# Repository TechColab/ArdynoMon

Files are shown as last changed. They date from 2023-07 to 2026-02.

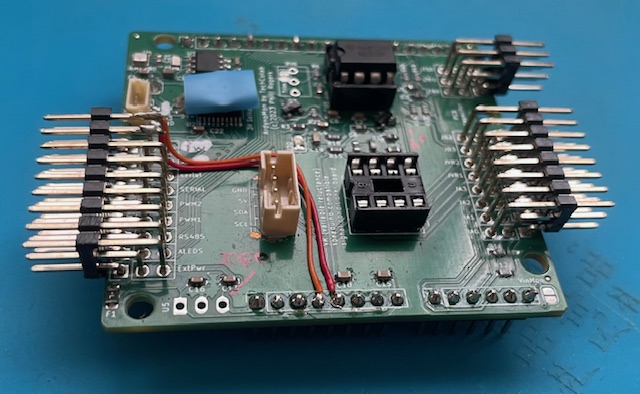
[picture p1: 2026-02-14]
ArdynoMon-ProtoMod.jpeg

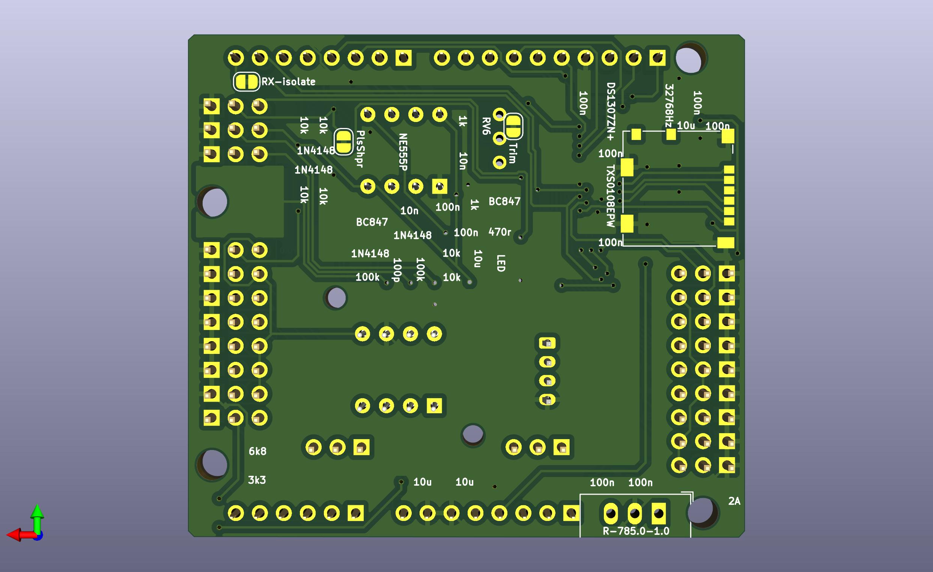
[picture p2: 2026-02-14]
ArdynoMon-B.jpg

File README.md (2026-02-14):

# ArdynoMon
Arduino shield for DIY dynos, engine monitoring &amp; more.  
Designed for monitoring & logging key aspects of an internal combustion engine for the purpose of R&D for my own Engine Management system. 
Aims to be the natural successor for the "Ardyno" shield https://ardyno.weebly.com/ with more input options & logging.  

Basically, it uses the Arduino's two interrupts to accuately record one or two channels of engine cycle events.  
While the original Ardyno would use one signal from an inertia drum roller & one signal from the ignition system, this ArdynoMon can alternatively be used to get both signals from different parts of the ignition system.  

# 2023-02-14 Revision 3.6 addresses all know issues.
    After some external interest (thank you) I've been nudged into refreshing this page.  
	I still get a bit lost with KiCAD files so if I've missed one from the upload, let me know.  
    Amusingly, I have recently used it to check th timing of a minimal EVSE (EV charger) I've built.  

# 2023-07-31 Don't use this version.
    Significant updated coming shortly to address the following issues with this version:  
	I accepted a subtitution of the transistors without realising that they have a different pinout.  
 	The RX going through the level shifter prevents in-situ programming.  
  	Better to choose the regulator on the Arduino *OR* the one on ArdynoMon shield, but not both!  
   	Both 1-Wire busses need a power pin as passive power is not always wanted.  

## 1.) updates from Ardyno Rev1  
	- drop A4 & A5 reducing on-board analogue inputs from 6 to 4.  
	+ frees I2C to go with UART & SPI  
	+ accept 1-wire digital temperature sensors (both 5V & 3.3V) bus powered or not  
	+ accept trigger from coil primary. Option for lo-V (5-12V COP) or hi-V (400V CDI/IDI)  
	+ accept trigger from 12V (& 5V) Hall effect sensors with suitable protection. Rising or Falling edge    
	+ option for VR conditioner / Opto-isolator plug-in board  
		E.g. in addition to coil primary trigger for measuring dwell time  
	+ gives 2 digital I/Os for PWM, servo, Dir+Step, analogue output etc.
		E.g. PWM eddie current brake & servo throttle  
		E.g. foot-switch to trigger logging time-stamp 'way-point'  
	+ better use of coastline with 3-pin 90-degree pin headers, can also use IDC ribbon cable connectors  
	+ all key signals are 3V & 5V  
	+ replace 555 timing C & R with 1nF (as close as poss) & 1k + optional 2M trim-pot for variable pulse width  
	+ put LED on output of 555 to aid diagnosing pick-ups which use it  
	= wider audience, upgradable, inline with YourDyno  

## 2.) additional monitoring features integrated
	+ uSD/TF on SPI, sharable with other SPI devices
	+ ambient humidity, air pressure, temperature on I2C  
	+ RTC on I2C  
	+ jumper option with resistor divider to measure vehicle battery voltage
	= fully integrated logger (not just ArdynoMon) better than existing one. Can share SPI, doesn't use analogue pins  

## 3.) designed-for optional ad-hoc add-ons
	drive individually addressable RGB LEDs for rev-counter & other indicators etc.
	serial logging via Bluetooth or WiFi module. On pigtails to get out of Faraday cage  
	current sensor on COP to find required dwell time - to one of the analogue inputs  
	RS485 bus for multi-drop peripheral/controller  
	1-wire: DS18b20, K-type thermocouple amplifiers, battery monitor  
	I2C: 24-bit ADC strain-guage amplifier, IMU  
	SPI: CAN bus?
	published (push-pull buffered) sync pulse from conditioned signal. For tacho, etc. (crank & cycle)  
	can drive high power COB LEDs via MOSFET for simple ignition strobe light  

# Uses:

Monitor the ignition trigger pick-up & the coil to capture the advance/retard curve of the CDI/IDI system.  
Monitor the coil primary to capture the dwell time variation of an induction (IDI) system.  
Monitor the RPM & drive an LED ring for rev-counter with MOSFET for rev-limmiter or auto-shift.  
Add supplimental injection system: N2O, H2O etc.

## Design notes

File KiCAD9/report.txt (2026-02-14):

Plotted to '/media/phill/Data/Documents/kicad/ArdynoMon/Gerbers/ArdynoMon-F_Cu.gbr'.
Plotted to '/media/phill/Data/Documents/kicad/ArdynoMon/Gerbers/ArdynoMon-B_Cu.gbr'.
Plotted to '/media/phill/Data/Documents/kicad/ArdynoMon/Gerbers/ArdynoMon-F_Silkscreen.gbr'.
Plotted to '/media/phill/Data/Documents/kicad/ArdynoMon/Gerbers/ArdynoMon-B_Silkscreen.gbr'.
Created Gerber job file '/media/phill/Data/Documents/kicad/ArdynoMon/Gerbers/ArdynoMon-job.gbrjob'.
Info: Done.
Info: Done.

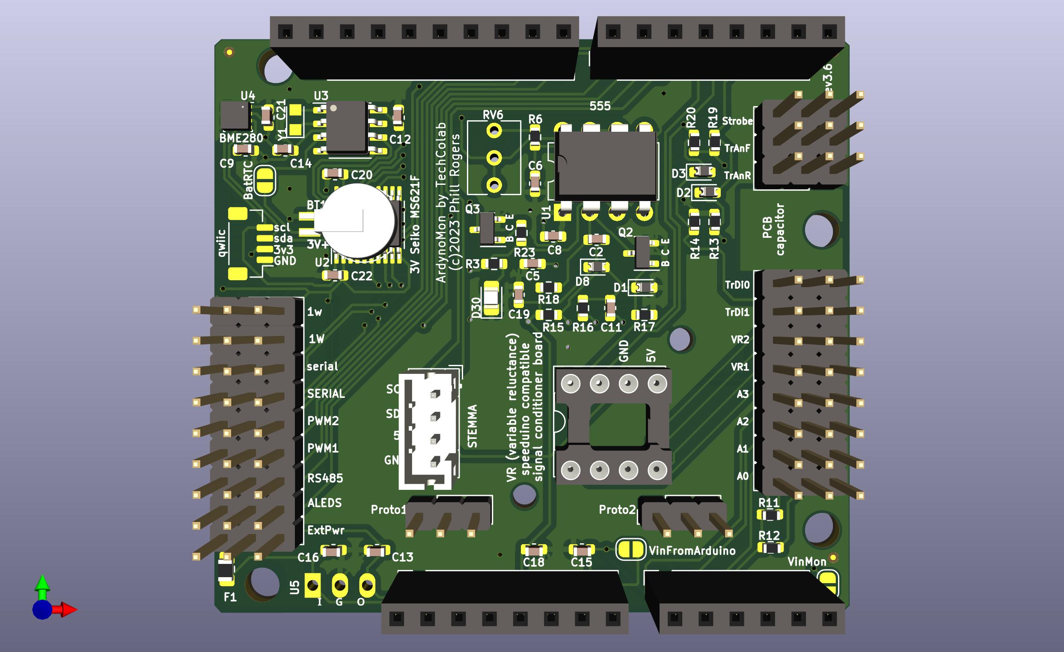
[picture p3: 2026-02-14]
ArdynoMon-F.jpg

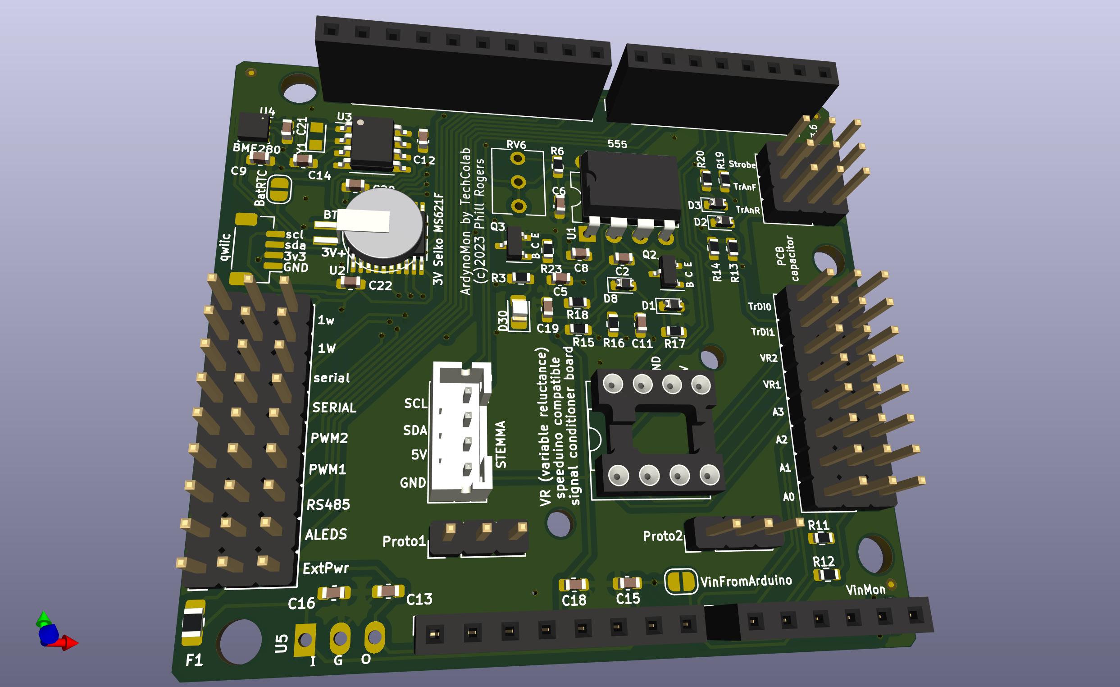
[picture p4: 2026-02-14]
ArdynoMon-Fangled.jpg

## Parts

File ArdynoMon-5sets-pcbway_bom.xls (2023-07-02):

PCBWay Bom Quotation, Product No.:T-1F6W473013A
Item # | *Designator | *Qty | Manufacturer | *Mfg Part # | Description / Value | *Package/Footprint | Mounting Type | *Unit Price(5 sets) | *Total | *Delivery Time | *Actual Purchase Mfg Part # | *PCBWay Note | Customer Reply | PCBWay Update
1 | BT1 | 1 |  |  | 3V Seiko MS621F | BatteryHolder_Seiko_MS621F | smt |  |  |  |  | [DNP不要贴];
2 | C11 | 1 | YAGEO |  | 100p | C_0603_1608Metric | smt | $0.058 | $0.290 |  | CC0603JRNPO9BN101
3 | C12, C13, C16, C20, C21, C22, C5, C8, C9 | 9 | YAGEO |  | 100n | C_0603_1608Metric | smt | $0.007 | $0.315 |  | CC0603KRX7R9BB104
4 | C14, C15, C18, C19 | 4 | YAGEO |  | 10u | C_0603_1608Metric | smt | $0.129 | $2.580 |  | CC0603MRX5R8BB106
5 | C2, C6 | 2 | YAGEO |  | 10n | C_0603_1608Metric | smt | $0.021 | $0.210 |  | CC0603KRX7R9BB103
6 | D1, D2, D3, D8 | 4 | Taiwan Semiconductor Corporation |  | 1N4148 | D_0603_1608Metric | smt | $0.286 | $5.720 | 7-10 Workdays | TS4148C RCG
7 | D30 | 1 | LITEON |  | LED | LED_0805_2012Metric_Pad1.15x1.40mm_HandSolder | smt | $0.233 | $1.165 |  | LTST-C191TBKT | Color: BLUE
8 | F1 | 1 | Littelfuse Inc. |  | 2A | Fuse_0805_2012Metric_Pad1.15x1.40mm_HandSolder | smt | $0.653 | $3.265 |  | 0805L200SLTHYR
9 | FID1, FID2, FID3 | 3 |  |  | Fiducial | Fiducial_0.5mm_Mask1mm | smt |  |  |  |  | [DNP不要贴];
10 | J11 | 1 |  |  | VR board | DIP-8_W7.62mm_Socket | tht |  |  |  |  | [DNP不要贴];
11 | J13 | 1 | Ckmtw |  | Proto | PinHeader_1x03_P2.54mm_Vertical | tht |  |  |  | B-2100S03P-A110 | [DNP不要贴];
12 | J14 | 1 | Molex |  | Micro_SD_Card_Det_Hirose_DM3AT | microSD_HC_Molex_104031-0811 | smt | $0.849 | $4.245 |  | 104031-0811
13 | J15 | 1 | Ckmtw |  | ExtPwr | PinHeader_1x03_P2.54mm_Vertical | tht |  |  |  | B-2100S03P-A110 | [DNP不要贴];
14 | J17 | 1 | HCTL |  | Power | PinSocket_1x08_P2.54mm_Vertical | tht |  |  |  | PM254-1-08-Z-8.5 | [DNP不要贴];
15 | J18 | 1 | XFCN |  | Analog | PinSocket_1x06_P2.54mm_Vertical | tht |  |  |  | PM254V-11-06-H85 | [DNP不要贴];
16 | J19 | 1 | HCTL |  | Digital/PWM | PinSocket_1x10_P2.54mm_Vertical | tht |  |  |  | PM254-1-10-Z-8.5 | [DNP不要贴];
17 | J20 | 1 | HCTL |  | Digital/PWM | PinSocket_1x08_P2.54mm_Vertical | tht |  |  |  | PM254-1-08-Z-8.5 | [DNP不要贴];
18 | J21 | 1 | JST Sales America Inc. |  | qwiic | JST_SH_BM04B-SRSS-TB_1x04-1MP_P1.00mm_Vertical | smt | $0.392 | $1.960 |  | BM04B-SRSS-TB(LF)(SN)
19 | J22 | 1 | JST Sales America Inc. |  | STEMMA | JST_PH_B4B-PH-K_1x04_P2.00mm_Vertical | tht | $0.202 | $1.010 |  | B4B-PH-K(LF)(SN)
20 | J23 | 1 | Ckmtw |  | serial | PinHeader_1x03_P2.54mm_Vertical | tht |  |  |  | B-2100S03P-A110 | [DNP不要贴];
21 | JA0 | 1 | Ckmtw |  | A0 | PinHeader_1x03_P2.54mm_Vertical | tht |  |  |  | B-2100S03P-A110 | [DNP不要贴];
22 | JA1 | 1 | Ckmtw |  | A1 | PinHeader_1x03_P2.54mm_Vertical | tht |  |  |  | B-2100S03P-A110 | [DNP不要贴];
23 | JA2 | 1 | Ckmtw |  | A2 | PinHeader_1x03_P2.54mm_Vertical | tht |  |  |  | B-2100S03P-A110 | [DNP不要贴];
24 | JA3 | 1 | Ckmtw |  | A3 | PinHeader_1x03_P2.54mm_Vertical | tht |  |  |  | B-2100S03P-A110 | [DNP不要贴];
25 | JD10 | 1 | Ckmtw |  | PWM2 | PinHeader_1x03_P2.54mm_Vertical | tht |  |  |  | B-2100S03P-A110 | [DNP不要贴];
26 | JD2 | 1 | Ckmtw |  | TrDi0 | PinHeader_1x03_P2.54mm_Vertical | tht |  |  |  | B-2100S03P-A110 | [DNP不要贴];
27 | JD23 | 1 | Ckmtw |  | SERIAL | PinHeader_1x03_P2.54mm_Vertical | tht |  |  |  | B-2100S03P-A110 | [DNP不要贴];
28 | JD3 | 1 | Ckmtw |  | TrDi1 | PinHeader_1x03_P2.54mm_Vertical | tht |  |  |  | B-2100S03P-A110 | [DNP不要贴];
29 | JD5 | 1 | Ckmtw |  | ALEDS | PinHeader_1x03_P2.54mm_Vertical | tht |  |  |  | B-2100S03P-A110 | [DNP不要贴];
30 | JD6 | 1 | Ckmtw |  | 1W1w | PinHeader_1x03_P2.54mm_Vertical | tht |  |  |  | B-2100S03P-A110 | [DNP不要贴];
31 | JD78 | 1 | Ckmtw |  | RS485 | PinHeader_1x03_P2.54mm_Vertical | tht |  |  |  | B-2100S03P-A110 | [DNP不要贴];
32 | JD9 | 1 | Ckmtw |  | PWM1 | PinHeader_1x03_P2.54mm_Vertical | tht |  |  |  | B-2100S03P-A110 | [DNP不要贴];
33 | JP1 | 1 |  |  | VinMon | SolderJumper-2_P1.3mm_Open_RoundedPad1.0x1.5mm | tht |  |  |  |  | [DNP不要贴];
34 | JP2 | 1 |  |  | BatRTC | SolderJumper-2_P1.3mm_Open_RoundedPad1.0x1.5mm | tht |  |  |  |  | [DNP不要贴];
35 | JP3 | 1 |  |  | Trim | SolderJumper-2_P1.3mm_Bridged_RoundedPad1.0x1.5mm | tht |  |  |  |  | [DNP不要贴];
36 | JTF0 | 1 | Ckmtw |  | TrAnF | PinHeader_1x03_P2.54mm_Vertical | tht |  |  |  | B-2100S03P-A110 | [DNP不要贴];
37 | JTR0 | 1 | Ckmtw |  | TrAnR | PinHeader_1x03_P2.54mm_Vertical | tht |  |  |  | B-2100S03P-A110 | [DNP不要贴];
38 | JTS0 | 1 | Ckmtw |  | Strobe | PinHeader_1x03_P2.54mm_Vertical | tht |  |  |  | B-2100S03P-A110 | [DNP不要贴];
39 | JVR1 | 1 | Ckmtw |  | VR1 | PinHeader_1x03_P2.54mm_Vertical | tht |  |  |  | B-2100S03P-A110 | [DNP不要贴];
40 | JVR2 | 1 | Ckmtw |  | VR2 | PinHeader_1x03_P2.54mm_Vertical | tht |  |  |  | B-2100S03P-A110 | [DNP不要贴];
41 | MH1, MH2, MH3, MH4 | 4 |  |  | MountingHole_3.2mm | MountingHole_3.2mm | tht |  |  |  |  | [DNP不要贴];
42 | Q2, Q3 | 2 | Nexperia USA Inc. |  | NPN | SOT-23 | smt | $0.034 | $0.340 |  | BC847,215
43 | R11 | 1 | YAGEO |  | 6k8 | R_0603_1608Metric | smt | $0.031 | $0.155 |  | RC0603FR-076K8L
44 | R12 | 1 | YAGEO |  | 3k3 | R_0603_1608Metric | smt | $0.031 | $0.155 |  | RC0603FR-073K3L
45 | R13, R14, R15, R18, R19, R20 | 6 | YAGEO |  | 10k | R_0603_1608Metric | smt | $0.004 | $0.120 |  | RC0603FR-0710KL
46 | R16, R17 | 2 | YAGEO |  | 100k | R_0603_1608Metric | smt | $0.013 | $0.130 |  | RC0603FR-07100KL
47 | R23, R6 | 2 | YAGEO |  | 1k | R_0603_1608Metric | smt | $0.013 | $0.130 |  | RC0603FR-071KL
48 | R3 | 1 | YAGEO |  | 470r | R_0603_1608Metric | smt | $0.032 | $0.160 |  | RC0603FR-07470RL
49 | RV6 | 1 |  |  | Trim | Potentiometer_Vishay_T73XW_Horizontal | tht |  |  |  |  | [DNP不要贴];
50 | U1 | 1 | Texas Instruments |  | NE555P | DIP-8_W7.62mm | tht |  |  |  | NE555P | [DNP不要贴];
51 | U2 | 1 | Texas Instruments |  | TXS0108EPW | TSSOP-20_4.4x6.5mm_P0.65mm | smt | $0.681 | $3.405 |  | TXS0108EPWR
52 | U3 | 1 | Analog Devices Inc./Maxim Integrated |  | DS1307ZN+ | SOIC-8_3.9x4.9mm_P1.27mm | smt | $1.044 | $5.220 |  | DS1307ZN+
53 | U4 | 1 | Bosch Sensortec |  | BME280 | Bosch_LGA-8_2.5x2.5mm_P0.65mm_ClockwisePinNumbering | smt | $2.984 | $14.920 |  | BME280
54 | U5 | 1 | Recom Power |  | R-785.0-1.0 | Converter_DCDC_RECOM_R-78E-0.5_THT | tht |  |  |  | R-785.0-1.0 | [DNP不要贴];
55 | Y1 | 1 | Raltron Electronics |  | 32768Hz | Crystal_SMD_2012-2Pin_2.0x1.2mm_HandSoldering | smt | $1.023 | $5.115 | 7-10 Workdays | RT2012-32.768-6-TR
 |  |  |  |  |  |  |  | All Total | $50.610

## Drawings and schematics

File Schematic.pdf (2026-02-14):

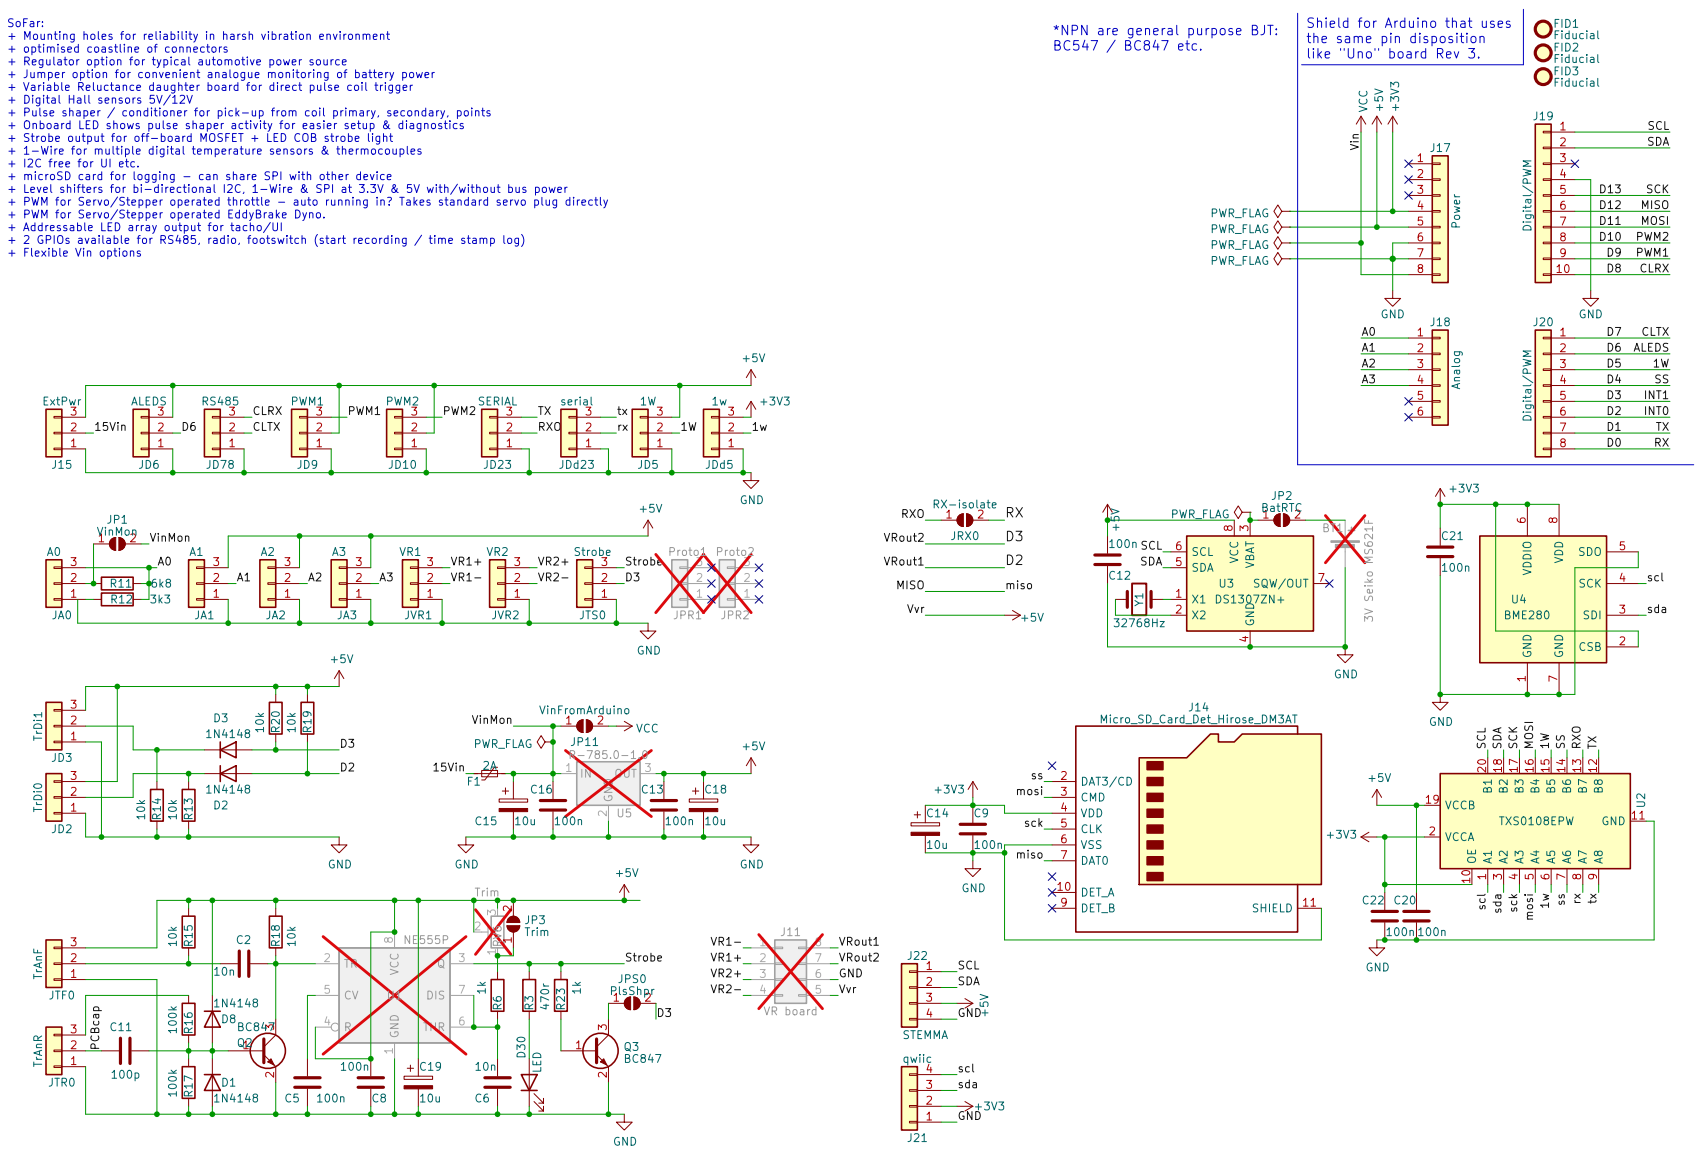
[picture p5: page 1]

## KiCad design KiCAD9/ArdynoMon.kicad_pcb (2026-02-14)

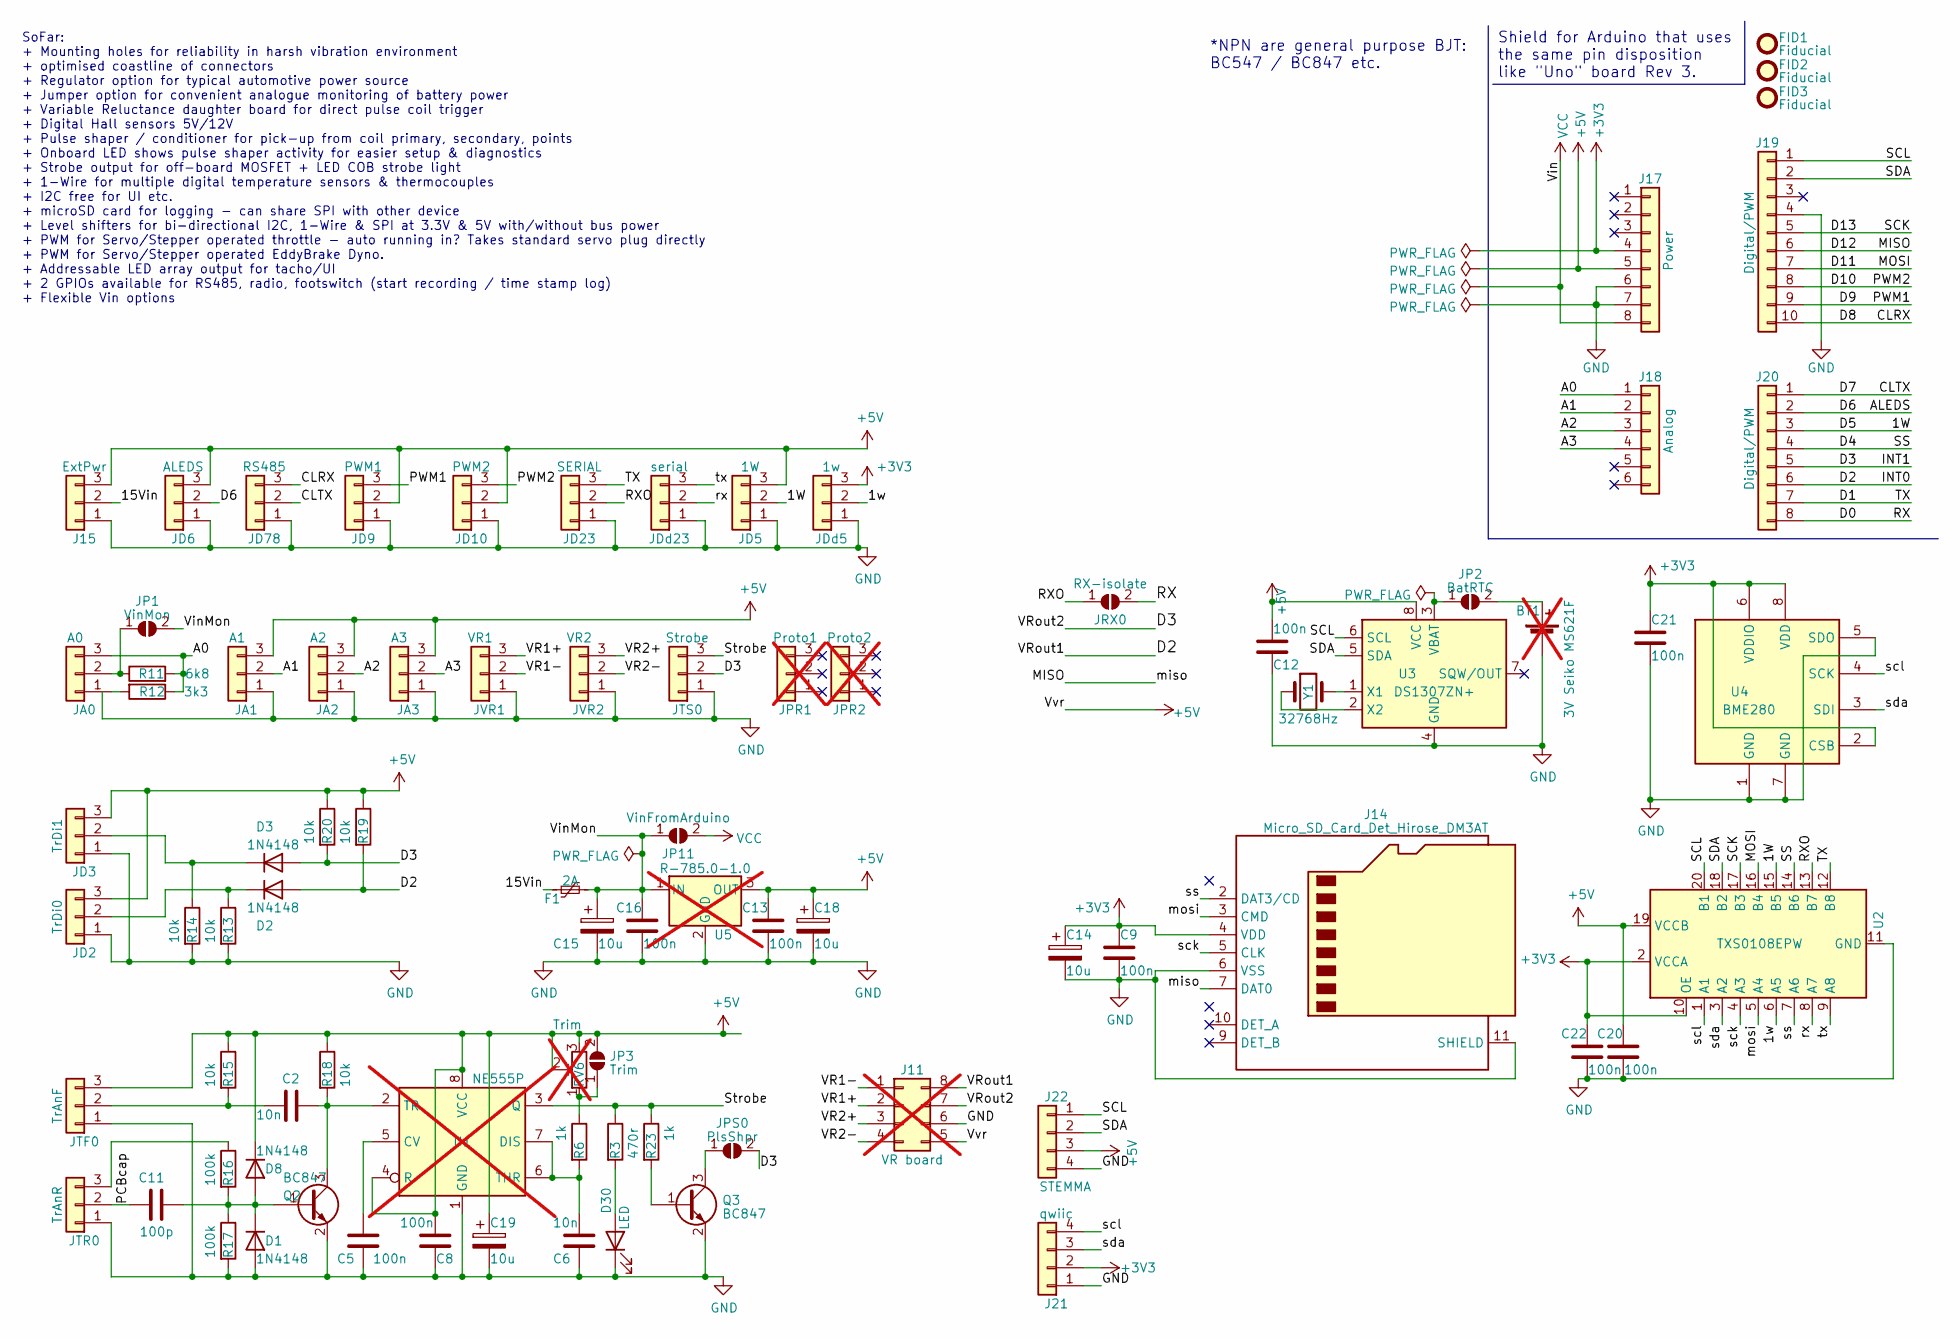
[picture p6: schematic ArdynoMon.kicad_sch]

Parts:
BT1: 3V Seiko MS621F; BatteryHolder_Seiko_MS621F; not fitted
C2, C6: 10n; C_0603_1608Metric; MFG Part Num GRM188R71E103KA01D
C5, C8, C9, C12, C13, C16, C20, C21, C22: 100n; C_0603_1608Metric; MFG Part Num 06033G104ZAT4A
C11: 100p; C_0603_1608Metric; MFG Part Num VJ0603Y101MXXCW1BC
C14, C15, C18, C19: 10u; C_0603_1608Metric; MFG Part Num GRM188R61E106MA73J
D1, D2, D3, D8: 1N4148; D_0603_1608Metric; MFG Part Num TS4148C RCG
D30: LED; LED_0805_2012Metric_Pad1.15x1.40mm_HandSolder; MFG Part Num LTST-C191TBKT
F1: 2A; Fuse_0805_2012Metric_Pad1.15x1.40mm_HandSolder; MFG Part Num 0805L200SLTHYR
FID1, FID2, FID3: Fiducial; Fiducial_0.5mm_Mask1mm
J11: VR board; DIP-8_W7.62mm_Socket; not fitted
J14: Micro_SD_Card_Det_Hirose_DM3AT; microSD_HC_Molex_104031-0811; MFG Part Num 104031-0831
J15: ExtPwr; PinHeader_1x03_P2.54mm_Vertical
J17: Power; PinSocket_1x08_P2.54mm_Vertical
J18: Analog; PinSocket_1x06_P2.54mm_Vertical
J19: Digital/PWM; PinSocket_1x10_P2.54mm_Vertical
J20: Digital/PWM; PinSocket_1x08_P2.54mm_Vertical
J21: qwiic; JST_SH_BM04B-SRSS-TB_1x04-1MP_P1.00mm_Vertical; MFG Part Num BM04B-SRSS-TB
J22: STEMMA; JST_PH_B4B-PH-K_1x04_P2.00mm_Vertical; MFG Part Num B4B-PH-K-S (LF)(SN)
JA0: A0; PinHeader_1x03_P2.54mm_Vertical
JA1: A1; PinHeader_1x03_P2.54mm_Vertical
JA2: A2; PinHeader_1x03_P2.54mm_Vertical
JA3: A3; PinHeader_1x03_P2.54mm_Vertical
JD2: TrDi0; PinHeader_1x03_P2.54mm_Vertical
JD3: TrDi1; PinHeader_1x03_P2.54mm_Vertical
JD5: 1W; PinHeader_1x03_P2.54mm_Vertical
JD6: ALEDS; PinHeader_1x03_P2.54mm_Vertical
JD9: PWM1; PinHeader_1x03_P2.54mm_Vertical
JD10: PWM2; PinHeader_1x03_P2.54mm_Vertical
JD23: SERIAL; PinHeader_1x03_P2.54mm_Vertical
JD78: RS485; PinHeader_1x03_P2.54mm_Vertical
JDd5: 1w; PinHeader_1x03_P2.54mm_Vertical
JDd23: serial; PinHeader_1x03_P2.54mm_Vertical
JP1: VinMon; SolderJumper-2_P1.3mm_Open_RoundedPad1.0x1.5mm
JP2: BatRTC; SolderJumper-2_P1.3mm_Open_RoundedPad1.0x1.5mm
JP3: Trim; SolderJumper-2_P1.3mm_Bridged_RoundedPad1.0x1.5mm
JP11: VinFromArduino; SolderJumper-2_P1.3mm_Open_RoundedPad1.0x1.5mm
JPR1: Proto1; PinHeader_1x03_P2.54mm_Vertical; not fitted
JPR2: Proto2; PinHeader_1x03_P2.54mm_Vertical; not fitted
JPS0: PlsShpr; SolderJumper-2_P1.3mm_Bridged_RoundedPad1.0x1.5mm
JRX0: RX-isolate; SolderJumper-2_P1.3mm_Bridged_RoundedPad1.0x1.5mm
JTF0: TrAnF; PinHeader_1x03_P2.54mm_Vertical
JTR0: TrAnR; PinHeader_1x03_P2.54mm_Vertical
JTS0: Strobe; PinHeader_1x03_P2.54mm_Vertical
JVR1: VR1; PinHeader_1x03_P2.54mm_Vertical
JVR2: VR2; PinHeader_1x03_P2.54mm_Vertical
Q2, Q3: BC847; SOT-23; MFG Part Num BC847,215
R3: 470r; R_0603_1608Metric; MFG Part Num ESR03EZPF4700
R6, R23: 1k; R_0603_1608Metric; MFG Part Num ERJ-PA3F1001V
R11: 6k8; R_0603_1608Metric; MFG Part Num ERJPA3F6801V
R12: 3k3; R_0603_1608Metric; MFG Part Num ERJPA3F3301V
R13, R14, R15, R18, R19, R20: 10k; R_0603_1608Metric; MFG Part Num ERJPA3F1002V
R16, R17: 100k; R_0603_1608Metric; MFG Part Num ERJ-PA3F1003V
RV6: Trim; Potentiometer_Vishay_T73XW_Horizontal; not fitted
U1: NE555P; DIP-8_W7.62mm; not fitted
U2: TXS0108EPW; TSSOP-20_4.4x6.5mm_P0.65mm; MFG Part Num TXS0108EPW
U3: DS1307ZN+; SOIC-8_3.9x4.9mm_P1.27mm; MFG Part Num DS1307ZN+T&R
U4: BME280; Bosch_LGA-8_2.5x2.5mm_P0.65mm_ClockwisePinNumbering; MFG Part Num BME280
U5: R-785.0-1.0; Converter_DCDC_RECOM_R-78E-0.5_THT; not fitted
Y1: 32768Hz; Crystal_SMD_2012-2Pin_2.0x1.2mm_HandSoldering; MFG Part Num RT2012-32.768-6-TR

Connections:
+3V3: C9.1, C14.1, C21.1, C22.1, J14.4 (VDD), J17.4, J21.2, JDd5.3, U2.2 (VCCA), U2.10 (OE), U4.2 (CSB), U4.6 (VDDIO), U4.8 (VDD)
+5V: C8.1, C12.1, C13.1, C18.1, C19.1, C20.1, D8.1 (K), J11.5, J15.3, J17.5, J22.3, JA1.3, JA2.3, JA3.3, JD2.3, JD3.3, JD5.3, JD6.3, JD9.2, JD10.2, JP3.2 (B), JTF0.3, R15.1, R18.1, R19.1, R20.1, RV6.2, RV6.3, U1.4 (R), U1.8 (VCC), U2.19 (VCCB), U3.8 (VCC), U5.3 (OUT)
/1W: J20.3, JD5.2, U2.15 (B5)
/1w: JDd5.2, U2.6 (A5)
/15Vin: F1.1, J15.2
/A0: J18.1, JA0.3, R11.2, R12.1
/A1: J18.2, JA1.2
/A2: J18.3, JA2.2
/A3: J18.4, JA3.2
/ALEDS: J20.2, JD6.2
/CLRX: J19.10, JD78.3
/CLTX: J20.1, JD78.2
/D0: J20.8, JRX0.2 (B)
/D1: J20.7, JD23.3, U2.12 (B8)
/D2: D2.2 (A), J11.8, J20.6, R19.2
/D3: D3.2 (A), J11.7, J20.5, JPS0.2 (B), JTS0.2, R20.2
/D4: J20.4, U2.14 (B6)
/D9: J19.9, JD9.3
/D10: J19.8, JD10.3
/D11: J19.7, U2.16 (B4)
/D12: J14.7 (DAT0), J19.6
/D13: J19.5, U2.17 (B3)
/PCBcap: C11.1, JTR0.2
/RXO: JD23.2, JRX0.1 (A), U2.13 (B7)
/SCL: J19.1, J22.1, U2.20 (B1), U3.6 (SCL)
/SDA: J19.2, J22.2, U2.18 (B2), U3.5 (SDA)
/Strobe: JTS0.3, R3.1, R23.1, U1.3 (Q)
/VR1+: J11.2, JVR1.3
/VR1-: J11.1, JVR1.2
/VR2+: J11.3, JVR2.3
/VR2-: J11.4, JVR2.2
/VinMon: C15.1, C16.1, F1.2, JP1.2 (B), JP11.1 (A), U5.1 (IN)
/mosi: J14.3 (CMD), U2.5 (A4)
/rx: JDd23.2, U2.8 (A7)
/sck: J14.5 (CLK), U2.4 (A3)
/scl: J21.4, U2.1 (A1), U4.4 (SCK)
/sda: J21.3, U2.3 (A2), U4.3 (SDI)
/ss: J14.2 (DAT3/CD), U2.7 (A6)
/tx: JDd23.3, U2.9 (A8)
GND: BT1.2 (-), C5.2, C6.2, C8.2, C9.2, C12.2, C13.2, C14.2, C15.2, C16.2, C18.2, C19.2, C20.2, C21.2, C22.2, D1.2 (A), D30.1 (K), J11.6, J14.6 (VSS), J14.11 (SHIELD), J15.1, J17.6, J17.7, J19.4, J21.1, J22.4, JA1.1, JA2.1, JA3.1, JD2.1, JD3.1, JD5.1, JD6.1, JD9.1, JD10.1, JD23.1, JD78.1, JDd5.1, JDd23.1, JTF0.1, JTR0.1, JTS0.1, JVR1.1, JVR2.1, Q2.2 (E), Q3.2 (E), R13.2, R14.2, R17.2, U1.1 (GND), U2.11 (GND), U3.4 (GND), U4.1 (GND), U4.5 (SDO), U4.7 (GND), U5.2 (GND)
unnamed: JP2.1 (A), U3.3 (VBAT)
unnamed: BT1.1 (+), JP2.2 (B)
unnamed: C11.2, D1.1 (K), D8.2 (A), Q2.1 (B), R16.2, R17.1
unnamed: D2.1 (K), JD2.2, R13.1
unnamed: D3.1 (K), JD3.2, R14.1
unnamed: D30.2 (A), R3.2
unnamed: JA0.1, R12.2
unnamed: JA0.2, JP1.1 (A), R11.1
unnamed: JP3.1 (A), R6.1, RV6.1
unnamed: JPS0.1 (A), Q3.3 (C)
unnamed: C2.1, JTF0.2, R15.2
unnamed: JTR0.3, R16.1
unnamed: C2.2, Q2.3 (C), R18.2, U1.2 (TR)
unnamed: Q3.1 (B), R23.2
unnamed: C5.1, U1.5 (CV)
unnamed: C6.1, R6.2, U1.6 (THR), U1.7 (DIS)
unnamed: U3.1 (X1), Y1.2
unnamed: U3.2 (X2), Y1.1
VCC: J17.8, JP11.2 (B)

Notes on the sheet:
*NPN are general purpose BJT: BC547 / BC847 etc.
Shield for Arduino that uses the same pin disposition like "Uno" board Rev 3.
SoFar: + Mounting holes for reliability in harsh vibration environment + optimised coastline of connectors + Regulator option for typical automotive power source + Jumper option for convenient analogue monitoring of battery power + Variable Reluctance daughter board for direct pulse coil trigger + 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

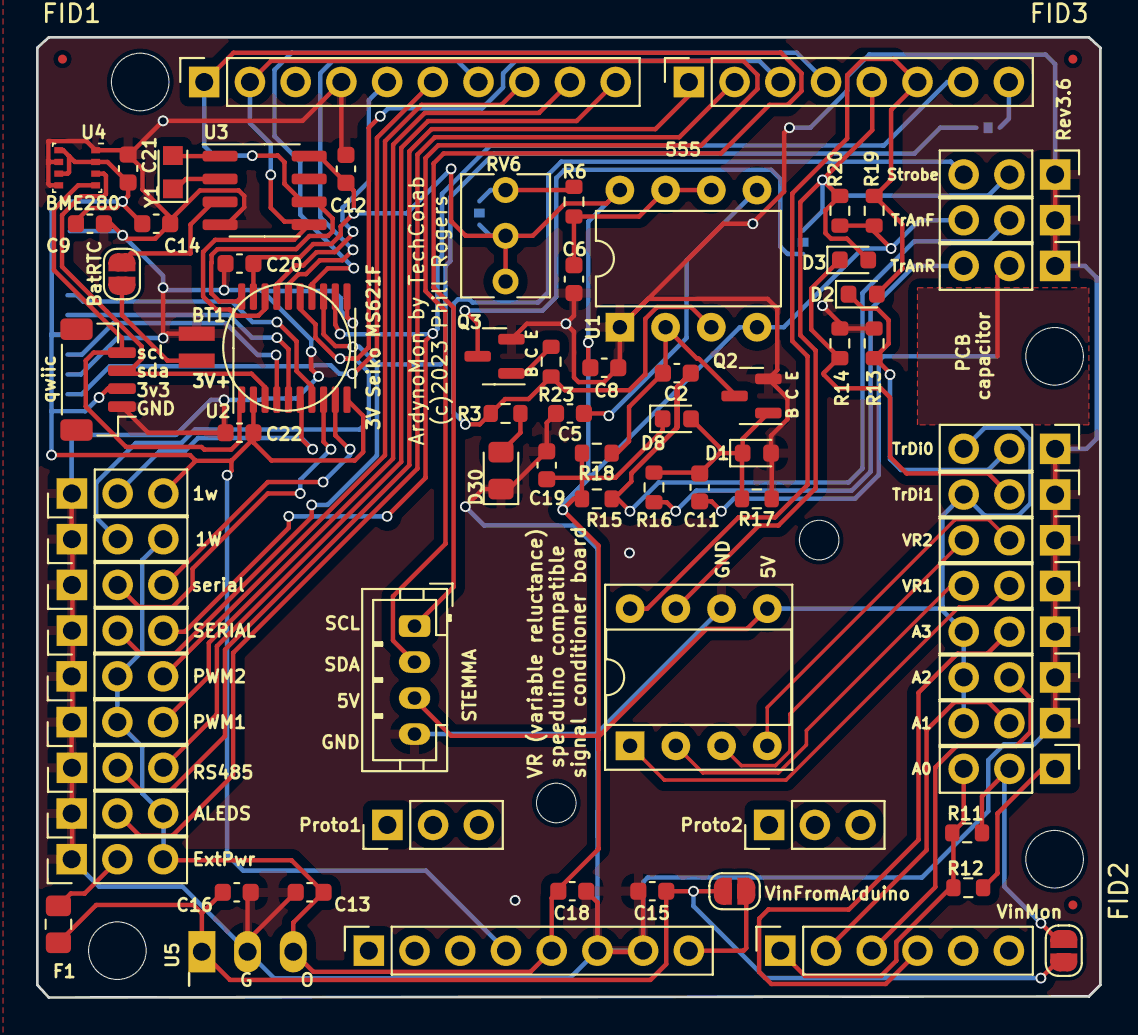
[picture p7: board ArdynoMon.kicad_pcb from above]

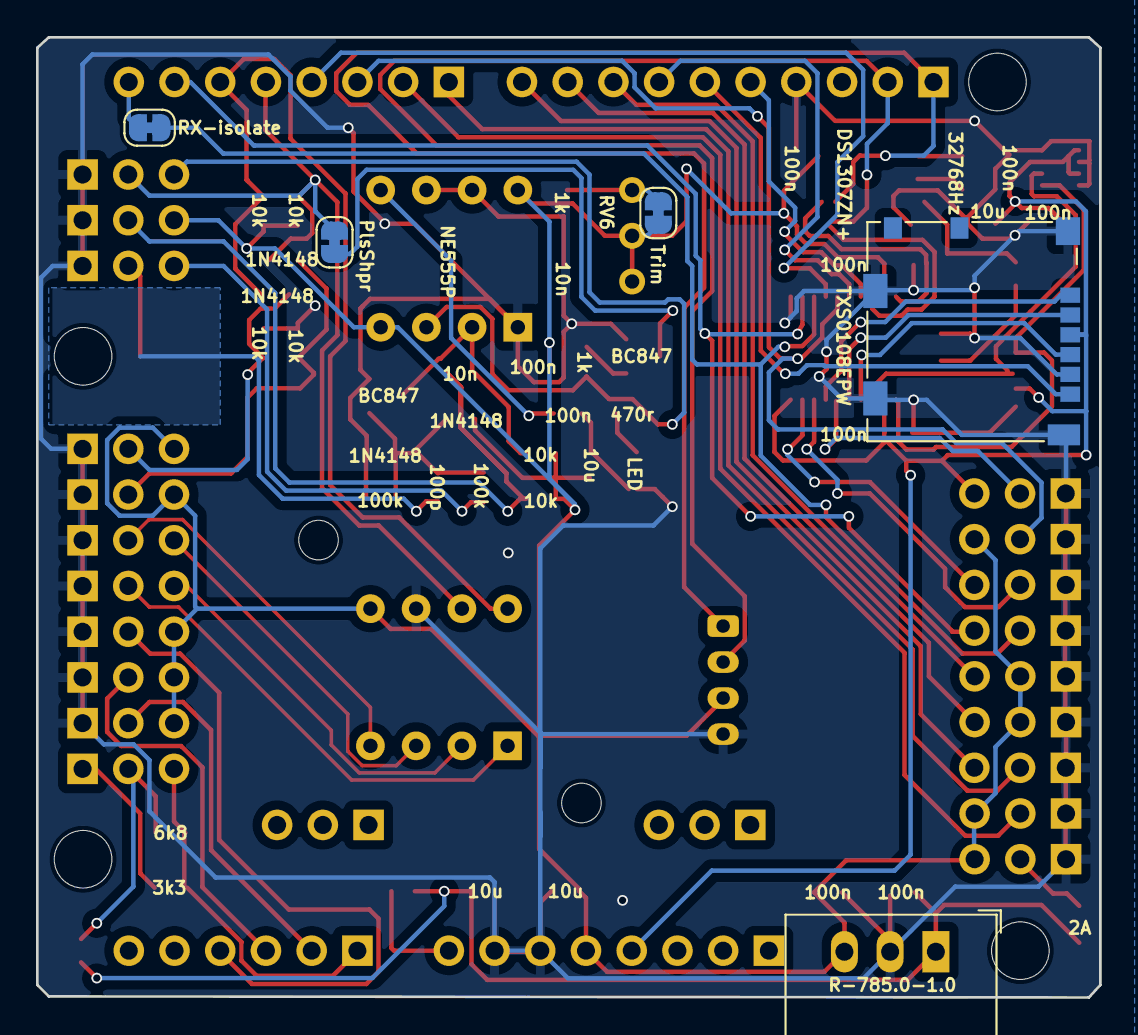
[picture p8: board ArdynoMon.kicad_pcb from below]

Board: 2 copper layers, 59.1 x 53.3 mm, 88 parts (5 on the bottom side), 59 nets.

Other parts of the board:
MH1, MH2, MH3, MH4: MountingHole_3.2mm

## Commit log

2026-02-14 Rev 3.6
    [ArdynoMon.kicad_pcb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]
2026-02-14 Photo of prototype with mods and 3-row 90-degree pin connectors

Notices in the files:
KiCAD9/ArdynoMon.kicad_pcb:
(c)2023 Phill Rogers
